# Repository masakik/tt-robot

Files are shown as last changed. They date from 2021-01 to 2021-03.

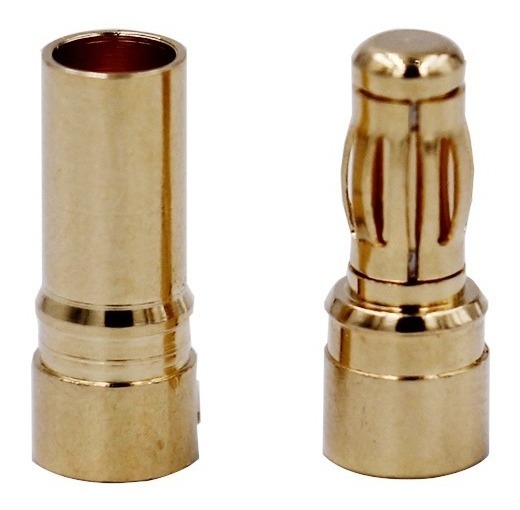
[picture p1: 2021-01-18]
images/conector 3,5mm.jpeg

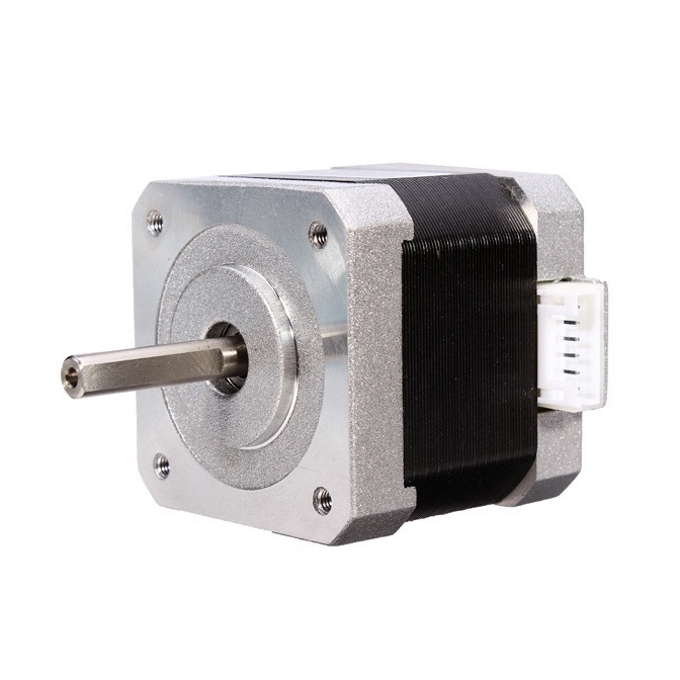
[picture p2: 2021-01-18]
images/motor de passo nema17.jpeg

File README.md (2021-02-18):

# tt-robot

## Steps

* Use arduino to control 2 spin motors (pwm fans from computer CPU) to put spin on balls, one for top and other for under spin;
* Read the RPM of motors
* use a stepper motor to feed balls to the spin motors

## TODO

* Programa de treino
* Beeps

## Updates

* Monitorando a voltagem da fonte de alimentação
* Substituido os motores de fan por ESC+BRUSHLESS
* Botão de pausa sem trava
* Sensor de bola com infravermelho
* Alimentador de bola como motor de passo mais potente (4,2kgf.cm) e driver A4988

## Parts

* Arduino nano ATmega328
* Driver A4988 para motor de passo
* Sensor infravermelho
* Motor De Passo Nema 17 4,2 Kgf.cm 12v 17hs4401, eixo 5mm
* Flange para motor de passo (disco inferior)
* 2 servos MG996R
* adaptador de disco plastico do servo: d20.5mm, parafuso soberba que veio junto do servo
* 2 motores A2212/13T, 1000KV
* 2 ESC HW30A
* anel de EVA para o disco

* display ??
* segundo arduino ??
* encoder rotativo ??

## Features

Robo lançador de bolas programável e cesta coletora realimentada. 

Ajustes:
* efeito (top e under spin);
* velocidade do lancamento
* direção (direita/esquerda, cima e baixo)
* frequência (15 a 90 bolas por minuto).

Outras características
* Botão de pausa/continue com debounce (A0)
* Todos os ajustes/controles são realizados pela porta Serial
* Ajustes de posição da cabeça por meio de servos 
* Lancamento de bola com ESC + motor brushless
* Beep de indicação
* Alimentação de 12V, conversor LM7805 para 5V
* Alimentador de bolas por meio de disco girante horizontal com 4 bolas por girando
* Contador de bolas lançadas
* Monitoramento da qualidade da fonte de alimentação (A2)

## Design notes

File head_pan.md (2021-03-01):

# PARTES

## Roda fake

#### 25/2/2021

* externo com raio de 20mm e espessura de 5.9mm ficou folgado.
* ajustado para 6 mas não impresso novamente

#### 25/2/2021

* impresso com raio menor. Ajustado na lixa

## Conexão tilt

#### 25/2/2021

* o pushrod fica do lado oposto do duto de cabos
* tem de resolver o espaço que fica quando o angulo é grande

#### 24/2/2021

* rolamento MR74ZZ: externo 7mm x interno 4mm x espessura 2.5mm
* pushrod terminal 1.3mm: furo 2mm
* barra de ligação tipo Z de 1.2mm, distancia do eixo do servo: 32mm
* canal de passagem de cabos

## Cabeça de lançamento

#### 25/2/2021

* rebaixado 2mm para centralizar o motor
* disco de EVA agora com 40mm de diâmetro, o motor ficou 4mm mais próximo
* feito recorte para saida da bola

#### 22/2/2021

* projeto da cabeça de lancamento
* impressão em draft, cerca de 3h, cinza
* fixacao do motor: parafuso m3x10mm

## Cabeça de Pan

#### 1/3/2021

* encurtado a curva para 20mm e entrada e saída para 9mm
* suporte para servo de tilt simplificado, com parafuso de 3mm para não usar apoio de borracha

#### 19/2/2021

* removido rebaixo do disco do servo superior, pois o suporte não estava ficando bom
* alinhado altura do suporte do servo superior com a ponta da curva para não ter necessidade de suporte
* criado suporte para servo de tilt na parte de trás. A ideia é ajudar a balancear um pouco o peso da parte frontal. Furo de 3mm e parafuso de 2.5mm com porca. Espaço da porca de 5mm
* o acionamento do tilt será por barra pushrod 1.2mm no braço de plástico do servo e conector na outra extremidade

#### Impressão 17/2/2021

* usado suporte giroide: ele grudou bastante, talvez o triangulo mesmo
* testado com suporte arvore: parece nao grudar bem, perdeu uma parte da peça ficando inutilizado em uns 10% da impressão.
* suporte 45%: talvez o 60 mesmo
* Cura: h0.20/E200/M60/25%/pla easyfill/vermelho/Parede1.2

* espessura: 0.20
* temp: 195/60
* cor: vermelho
* Material: pla easyfill
* disco do servo é de 20.5 mm, base foi feito com rebaixo de 20mm e 1mm de profundidade. Talvez 2 mm fosse melhor
* essa parte da impressão não ficou boa. Talvez outro suporte

## Conexão Pan

* A parte inferior tem de colocar um espaçador para fixação 

#### 17/2/2021

* Impresso sem suporte: ficou ruim a trava do meio mas não é grave
* Precisa de suporte
* o diametro livre ficou em 52 mm (1 mm de folga): ficou largo, acho que dá para deixar 0,5 mm de folga
* Cura: h0.15/E200/M60/pla easyfill/vermelho/parede1.5/suporte

### Config

* Tentar: Cura:h0.2/E195/M60/Sup/Parede1.2
* pla easyfill/vermelho
* 

## Suporte do servo

## presilha do pescoço

## disco do FEEDER

## pescoço inferior

## pé do pescoço inferior

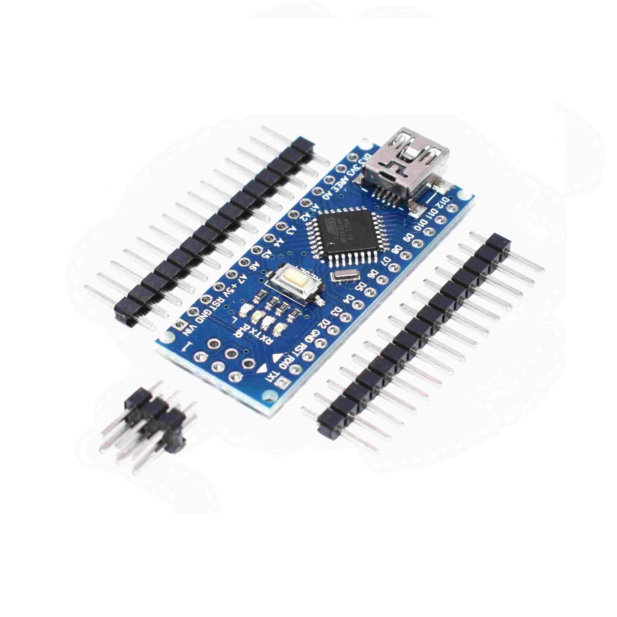
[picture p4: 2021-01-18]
images/Arduino-Nano-R3.jpeg

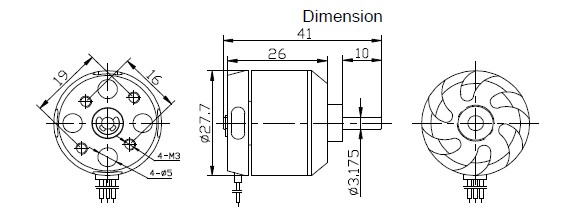
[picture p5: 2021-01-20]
images/a2212 size.jpeg

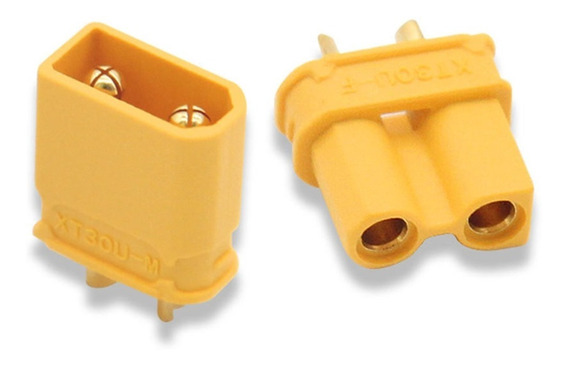
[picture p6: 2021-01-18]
images/conector xt30.jpeg

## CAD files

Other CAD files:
disco.dxf

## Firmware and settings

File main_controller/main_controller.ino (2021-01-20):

// Included libraries from library manager
#include <AccelStepper.h>
#include <Cmd.h>
#include <timer.h>
#include <timerManager.h>
#include <Servo.h>

#include "Scmd.h"

// Servos *************************************************
#define TOP_PIN 9
#define UNDER_PIN 10
#define AZIMUTE_PIN 11
#define ELEVATION_PIN 12
Servo azimute;
Servo elevation;
Servo top;
Servo under;

// Sensor de bola com modulo infravermelho ****************
unsigned int ball_freq = 60; // bolas por minuto
#define BALL_FREQ_MIN 15
#define BALL_FREQ_MAX 90

#define BALL_SENSOR_PIN A1       // o sensor envia LOW se detectou bola, então a lógica é invertida
#define BALL_SENSOR_DEBOUNCE 200 // debounce do sensor de bola (ms)

unsigned int ball_interval = 60000 / ball_freq;
unsigned long ball_prev_time = millis();
unsigned long ball_current_time;
bool ball_prev_state = 0;
unsigned int ball_counter = 0;
bool ball_soft_pause = true;

// motor de passo ***************************************
#define STEP_PIN 2
#define DIR_PIN 3
#define FEEDER_DELAY 250 // continua girando por mais um tempo (ms)
#define SPEED 200 // velocidade nominal de rotação (em pps)
unsigned long pause_btn_prev_time = millis();
AccelStepper feeder(AccelStepper::DRIVER, STEP_PIN, DIR_PIN);

// Botão de pausa do feeder ******************************
#define FEEDER_PAUSE_PIN A0     // pino do botão de pausar o ballFeeder
#define FEEDER_PAUSE_DEBOUNCE 500 // debounce do botão de pause (ms)


// Botão do buzzer
#define BUZZER_PIN A3
#include "Sound.h"
Sound sound(BUZZER_PIN);

// timers *************************************************
Timer timerPrintStatus;

// Auxiliar para Serial.print
char buffer[100];

// PSU voltage measure
#define VCC_MONITOR_PIN A2
unsigned int vcc_monitor;
float vcc_adj = 1.247; // vcc_multimetro/valor_lido


// Programação ********************************************

typedef struct {
  int top, under, elev, azim;
} Head;

Head pgm;
Head ps1_sp3_sn0 = {20, 20, 10, 10};

typedef struct {
  float vcc_adj;
} Config;

Config cfg;

// ********************************************************
void setup(void)
{
  // start serial port
  Serial.begin(9600);
  Serial.println("Table Tennis Robot");

  // config
  cfg.vcc_adj = vcc_adj;

  // programa
  pgm = ps1_sp3_sn0;

  // servos
  top.attach(TOP_PIN);
  under.attach(UNDER_PIN);
  azimute.attach(AZIMUTE_PIN);
  elevation.attach(ELEVATION_PIN);

  // Stepper
  feeder.setMaxSpeed(1000.0);
  feeder.setSpeed(SPEED);
  pinMode(FEEDER_PAUSE_PIN, INPUT_PULLUP);

  // sensor de bola
  pinMode(BALL_SENSOR_PIN, INPUT);

  // cmdSerial
  cmdInit(&Serial);
  cmdAdd("help", cmdHelp);
  cmdAdd("pgm", cmdProgram);
  cmdAdd("freq", cmdFreq);
  cmdAdd("pause", cmdFeederPause);
  cmdAdd("cont", cmdFeederCont);
  cmdAdd("status", cmdStatus);
  cmdAdd("top", cmdTopSpin);
  cmdAdd("under", cmdUnderSpin);
  //cmdAdd("elev", cmdElevation);
  //cmdAdd("azim", cmdAzimute);

  // timers
  timerPrintStatus.setInterval(10000);
  timerPrintStatus.setCallback(cmdStatus);

  TimerManager::instance().start();

  // vcc monitor
  pinMode(VCC_MONITOR_PIN, INPUT);

  // Sound
  sound.play(SOUND_MI, 1000);
}

// Main function ***************************
void loop(void)
{
  cmdPoll();
  TimerManager::instance().update();
  feeder.runSpeed();
  pollBallSensor();
  pollPauseBtn();
  pollBallFeed();
}

void cmdHelp(int arg_cnt, char **args)
{
  Serial.println("status");
  Serial.println("pgm 1..9");
  Serial.println("pause");
  Serial.println("cont");
  sprintf(buffer, "freq %i..%i (bolas por minuto)", BALL_FREQ_MIN, BALL_FREQ_MAX);
  Serial.println(buffer);
  Serial.println("top 0..100 (%)");
  Serial.println("under 0..100 (%)");

  // futuros
  Serial.println("elev -30..30 (graus)");
  Serial.println("azim -30..30 (graus)");
}

void cmdProgram(int arg_cnt, char **args)
{
  int pgm = 1;
  if (arg_cnt > 1)
  {
    pgm = cmdStr2Num(args[1], 10);
  }
  Serial.print("pgm ");
  Serial.println(pgm);
}

void cmdFreq(int arg_cnt, char **args)
{
  if (arg_cnt > 1)
  {
    ball_freq = max(min(cmdStr2Num(args[1], 10), BALL_FREQ_MAX), BALL_FREQ_MIN); // limita entre BALL_FREQ_MIN e BALL_FREQ_MAX
    ball_interval = 60000 / ball_freq;
  }
  Serial.print("freq ");
  Serial.println(ball_freq);
}

void cmdTopSpin(int arg_cnt, char **args)
{
  if (arg_cnt > 1)
  {
    top.write(max(min(cmdStr2Num(args[1], 10), 100), 0));
  }
  sprintf(buffer, "Top %i%%", top.read());
  Serial.println(buffer);
}

void cmdUnderSpin(int arg_cnt, char **args)
{
  if (arg_cnt > 1)
  {
    under.write(max(min(cmdStr2Num(args[1], 10), 100), 0));
  }
  sprintf(buffer, "Under %i%%", under.read());
  Serial.println(buffer);
}

void cmdFeederPause(int arg_cnt, char **args)
{
  ball_soft_pause = true;
  sound.pause();
}

void cmdFeederCont(int arg_cnt, char **args)
{
  ball_soft_pause = false;
  sound.pause();
}

void cmdStatus(int arg_cnt, char **args)
{
  vccMonitor();
  sprintf(buffer, "run: %i; count %i; freq %i; top %i%%; under %i%%; vcc %i",
          !ball_soft_pause, ball_counter, ball_freq,
          top.read(),
          under.read(),
          vcc_monitor
         );
  Serial.println(buffer);
}

void cmdStatus() {
  cmdStatus(0, 0);
}

void vccMonitor()
{
  unsigned int sum = 0;
  for (int i = 0; i < 20; i++)
  {
    sum = sum + analogRead(VCC_MONITOR_PIN);
  }
  vcc_monitor = map(sum / 20, 0, 1023, 0, 13000) * cfg.vcc_adj;
}


/**
   Verifica o sensor de bola se foi lançado ou não
   Como não tem interrupção disponível utilizou-se uma variável de estado.
   O lancamento é na borda de subida.
   Como a lógica é invertida vamos corrigir isso na leitura.
   Incrementa o contador de bolas
   (Utiliza debounce para minimizar repeticoes mas parece estar com problemas)
*/
void pollBallSensor()
{
  // verifica se lancou bola
  if ((!digitalRead(BALL_SENSOR_PIN) != ball_prev_state))
  {
    if ((ball_prev_state == LOW)  & (millis() - ball_current_time > BALL_SENSOR_DEBOUNCE))
    {
      ball_prev_state = HIGH;
      ball_current_time = millis();
      ball_counter++;

      int top_degree = random(0, 100);
      top.write(top_degree);
      under.write(top_degree);
      Serial.println(top_degree);
    }
    else
    {
      ball_prev_state = LOW;
    }
  }
}

/**
   Verifica se o botão de pause foi pressionado e muda o estado de pausa
   Como ele é pull_up, compara com LOW
*/
void pollPauseBtn()
{
  if ((digitalRead(FEEDER_PAUSE_PIN) == LOW) && (millis() - pause_btn_prev_time > FEEDER_PAUSE_DEBOUNCE))
  {
    ball_soft_pause = !ball_soft_pause;
    pause_btn_prev_time = millis();
    Serial.println("Botão de pausa pressionado");
    Serial.print("run ");
    Serial.println(!ball_soft_pause);
    sound.pause();
  }
}

/**
   Lança bola a cada intervalo de tempo com a opção de pausa
*/
void pollBallFeed()
{
  // vamos verificar o intervalo de lançamento && soft pause
  if (((millis() - ball_prev_time) > ball_interval) && !ball_soft_pause)
  {
    // se passou intervalo gira
    feeder.setSpeed(SPEED);
    ball_prev_time = ball_current_time;
  }
  else if (millis() - ball_prev_time > FEEDER_DELAY)
  {
    // depois de começar a girar vamos aguardar um pouco antes de parar
    // assim a bola se afasta do sensor evitando ler a mesma bola
    feeder.setSpeed(0);
  }
}

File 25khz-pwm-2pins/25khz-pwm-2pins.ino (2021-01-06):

//https://forum.arduino.cc/index.php?topic=633800.0

//PWM output @ 25 kHz, only on pins 9 and 10.
// Output value should be between 0 and 320, inclusive.
void analogWrite25k(int pin, int value)
{
  switch (pin)
  {
  case 9:
    OCR1A = value;
    break;

  case 10:
    OCR1B = value;
    break;

  default: // no other pin will work
    break;
  }
}

void setup() // Configure Timer 1 for PWM @ 25 kHz.
{
  TCCR1A = 0;            // undo the configuration done by...
  TCCR1B = 0;            // ...the Arduino core library
  TCNT1 = 0;             // reset timer
  TCCR1A = _BV(COM1A1)   // non-inverted PWM on ch. A
           | _BV(COM1B1) // same on ch; B
           | _BV(WGM11); // mode 10: ph. correct PWM, TOP = ICR1
  TCCR1B = _BV(WGM13)    // ditto
           | _BV(CS10);  // prescaler = 1
  ICR1 = 320;            // TOP = 320
  // Set the PWM pins as output.
  pinMode(9, OUTPUT);
  pinMode(10, OUTPUT);
}

void loop()
{
  // Just an example:
  analogWrite25k(9, 110);
  analogWrite25k(10, 210);
  for (;;)
    ; // infinite loop
}

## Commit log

2021-01-07 incluindo timer manager
2021-01-08 trocando comportamento do botao de pause
2021-01-11 rename de variaveis
2021-01-13 incluindo desenho cad
    [disco.dxf]
2021-01-13 incluindo fritzing
    [main_board.fzz]
2021-01-13 adequando nomes de variaveis
2021-01-14 testes no fritzing
    [main_board.fzz, main_board_pro_mini.fzz]
2021-01-15 trocando fan por servo
2021-01-18 rename de funcoes
2021-01-20 inicio do desenho do head
    [disco.dxf]
